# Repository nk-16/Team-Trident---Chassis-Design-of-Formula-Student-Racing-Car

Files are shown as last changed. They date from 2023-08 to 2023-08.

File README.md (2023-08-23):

# Team-Trident---Chassis-Design-of-Formula-Student-Racing-Car

<div style="text-align: justify;">
This project is under  Team Trident, SAE Collegiate Club, IIT(BHU), Varanasi, for the SUPRA SAE competition. This is based on the designing, simulation, and manufacturing of chassis.
</div>

<br>

* **Designing**  <div style="text-align: justify;">I contributed to chassis design in SOLIDWORKS. I learned about new features like planes, weldments, corner treatments, and 3D sketches. Before designing, we went through the rulebook of SUPRA SAE and understood all the constraints so we could design according to them.</div>

<div align="center">
  
</div>

<br>

* **Simulation** <div style="text-align: justify;">I contributed to the chassis simulation in Ansys Mechanical using Finite Element Analysis (FEA) to get stress-strain properties of the chassis. We did front impact testing, side impact testing, and rear impact testing and did hand-in calculations to verify Ansys results.</div>



<br>

* **Manufacturing** <div style="text-align: justify;">  After finalizing the chassis' design and getting suitable results from the simulation, we proceed to its manufacturing. We used AISI 1018 steel pipes and Manual Arc Welding to weld them.</div>



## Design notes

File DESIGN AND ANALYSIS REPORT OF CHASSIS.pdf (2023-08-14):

## DESIGN AND ANALYSIS REPORT OF CHASSIS

Abstract — This Design Report mainly analyzes the Formula Student Racing Car chassis. This chassis is designed by conforming to the rules of SUPRA SAE 2023. The chassis frame is the main structural component to which all the other parts are attached. The chassis frame acts as the skeleton of the automobile, so it should withstand various load conditions. FEA Analysis conforms to the ability to assess the forces and safety of design before manufacturing. The material Preferred for this chassis is AISI 1018, which has good strength and ductility and low weight and is economically viable. The analysis is done on standard Results to get the maximum strength and minimum weight possible. The software tool used for designing is SOLIDWORKS, and for analysis is ANSYS.

INTRODUCTION

The SAE competition comprises static and dynamic events, where the teams are judged based on various parameters, such as conforming to the rules, the vehicle's performance, teamwork, and vehicle compliance. The safety of the driver in the cockpit is of utmost importance. Hence, FEA analysis is carried out by considering various loads, such as bending, torsion, twisting, side impact, and front impact.

The FSAE chassis undergoes various forces during the dynamic event, and FEA analysis helps decide the manufacturing process needed to make the chassis as rigid as possible with minimal cost. Material selection also plays a vital role in strength and torsional rigidity. Therefore, the FEA analysis helps optimize the design and material selection to achieve the desired stiffness and stability while keeping costs low.

The paper focuses on the results of the analysis of the chassis used in the FSAE competition. Here we first explain the methodology of analysis and material property. Then, we will explain analysis calculations and simulation results when the chassis is used with front impact, side impact, rear impact, and torsional stiffness by the rules of the SUPRA SAE competition.

METHODOLOGY

The process typically begins with the team researching and analyzing the regulations set by SUPRA SAE, including weight and size limitations, safety requirements, and performance goals.
We then use this information to create a conceptual chassis design, refined and optimized using CAD software.

Once the design was finalized, we analyzed the chassis using finite element analysis (FEA) through ANSYS to ensure it met strength and stiffness requirements and safety regulations. FINITE ELEMENT ANALYSIS (FEA) [1] (https://www.ansys.com/en-in/blog/fundamentals-of-fea-meshing-for-structural-analysis) is carried out to determine the stiffness of the chassis frame before construction. Conventionally in FEA, the frame is subdivided into mesh elements. These meshes are further divided into nodes. Many elements are possible for a structure, and every choice the analyst makes can affect the results. The number, orientation, and size of elements and loads and boundary conditions are critical to obtaining meaningful and accurate values of chassis stiffness. While doing FEA, we chose tetrahedral elements for meshing and kept the average element size at 10 mm. We did conduct a mesh convergence study by also testing results at an element size of 5 mm. We didn't observe quite a deviation, so we finalized the element size to be kept as 10 mm for simplification in computation.

After finalizing the design, the designing team works with the manufacturing team to ensure that the chassis can be produced within the specified budget and manufactured to the highest quality Standards.

After our research, we optimized the dimensions of the chassis.

### 1. Wheelbase = 1589.14 mm 2. Mass = 32.85 kg 3. Material = AISI 1018

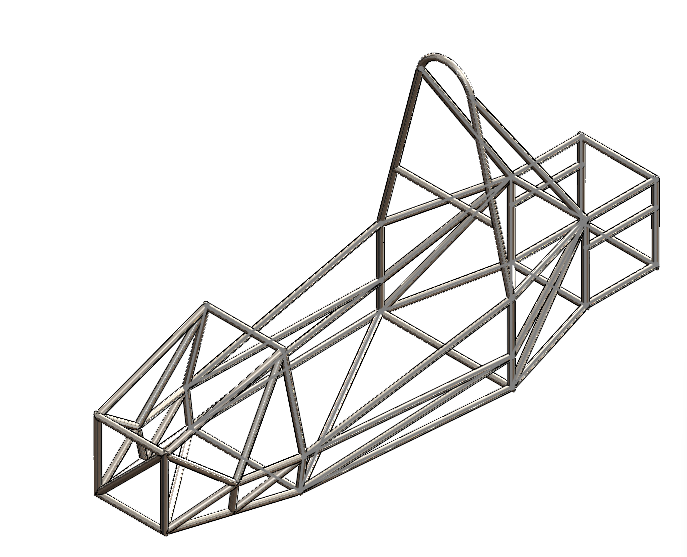
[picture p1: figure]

Fig 1: Isometric view of chassis

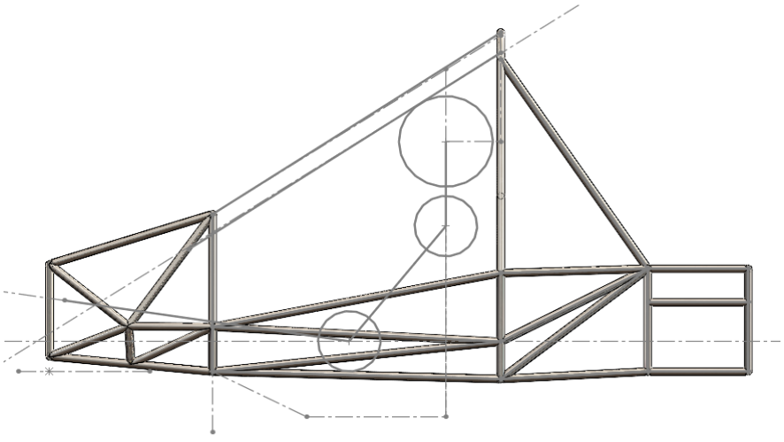
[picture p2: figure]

Fig 2.1: Side view of chassis with a sketch of 95th percentile man

DESIGN PROCESS

We began designing our chassis in September 2023. The Final draft and all analyses were completed by December 2023. The procurement of material and its manufacturing will be completed by February 2023. Hence in this section, the stages of our design have been discussed in detail.

1.) Understanding constraints and subsequent steps

We first go through the rulebook of SUPRA SAE and understand the constraints like:-

- Triangulation of all members in chassis
- Height of main hoop and front hoop
- Minimum wheelbase
- Size of side impact members
- Angles of the main hoop and front hoop
- Distance between firewall and engine
- Specifications of 95th percentile male and 50 mm rule
1.1) We started our sketch-making wheelbase and respective planes for the main hoop, front hoop, rear hoop, front bulkhead, and impact attenuator. Initially, we took a wheelbase of 1800 mm, but later, altering the positions of the hoops and changing the leg angle to 95th percentile male, we finalized at 1589.14 mm. Then we draw all

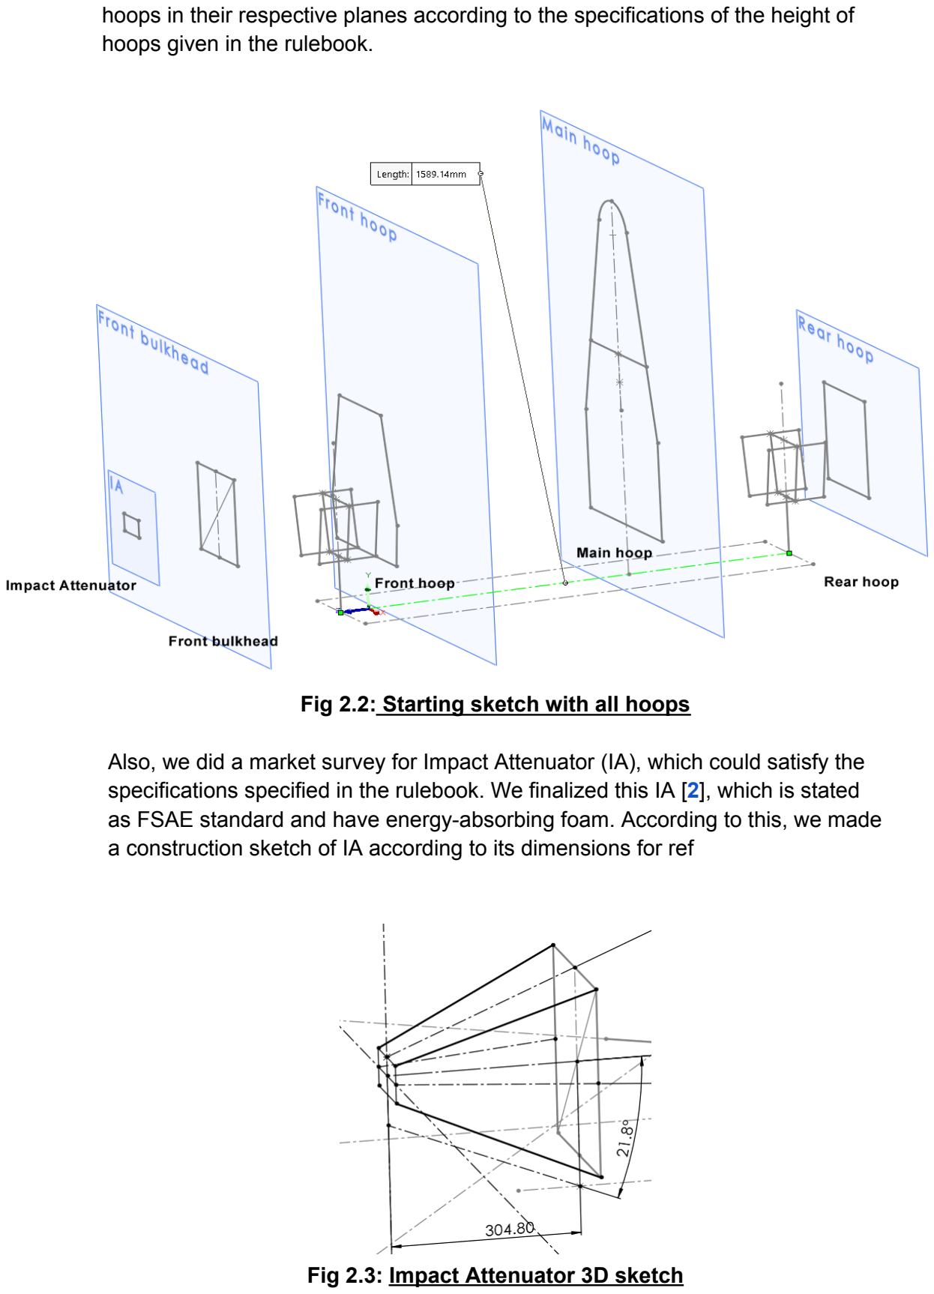
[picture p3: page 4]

hoops in their respective planes according to the specifications of the height of hoops given in the rulebook.

Fig 2.2: Starting sketch with all hoops

Also, we did a market survey for Impact Attenuator (IA), which could satisfy the specifications specified in the rulebook. We finalized this IA [2], (https://pdf.indiamart.com/impdf/16297415162/MY-4624662/fsae-spec-standard-impact-attenuator.pdf) which is stated as FSAE standard and have energy-absorbing foam. According to this, we made a construction sketch of IA according to its dimensions for ref

Fig 2.3: Impact Attenuator 3D sketch

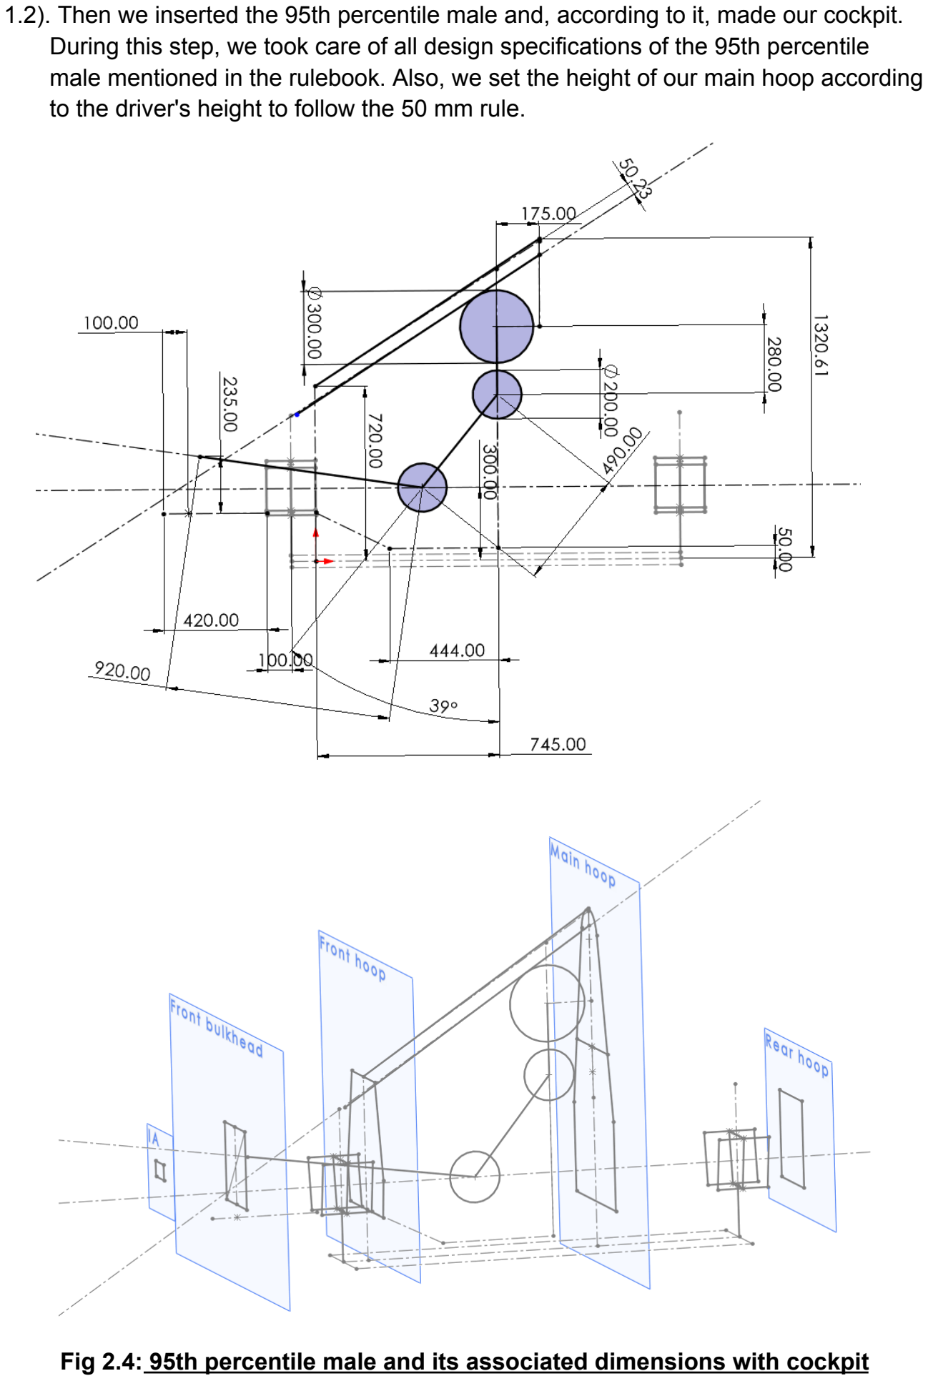
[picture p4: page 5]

1.2). Then we inserted the 95th percentile male and, according to it, made our cockpit. During this step, we took care of all design specifications of the 95th percentile male mentioned in the rulebook. Also, we set the height of our main hoop according to the driver's height to follow the 50 mm rule.

Fig 2.4: 95th percentile male and its associated dimensions with cockpit

1.3) We draw the trusses in between hoops. We first draw the side impact
members between the main and front hoops to complete the cockpit. After this, we complete the trusses between other hoops. The trusses between the front hoop and front bulkhead have been altered after analysis of each cad model in ansys.

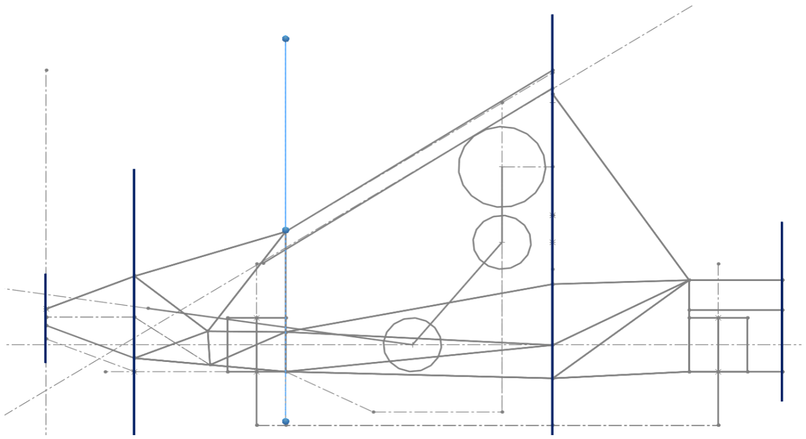
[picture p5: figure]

Fig 2.5: Side view of chassis sketch with a sketch of 95th percentile man

1.4) As per the rulebook, we use custom weldment profiles to have proper AISI 1018 pipes of the correct diameter and thickness. Then we do corner treatment using the trim/extend feature to refine all chassis corners.

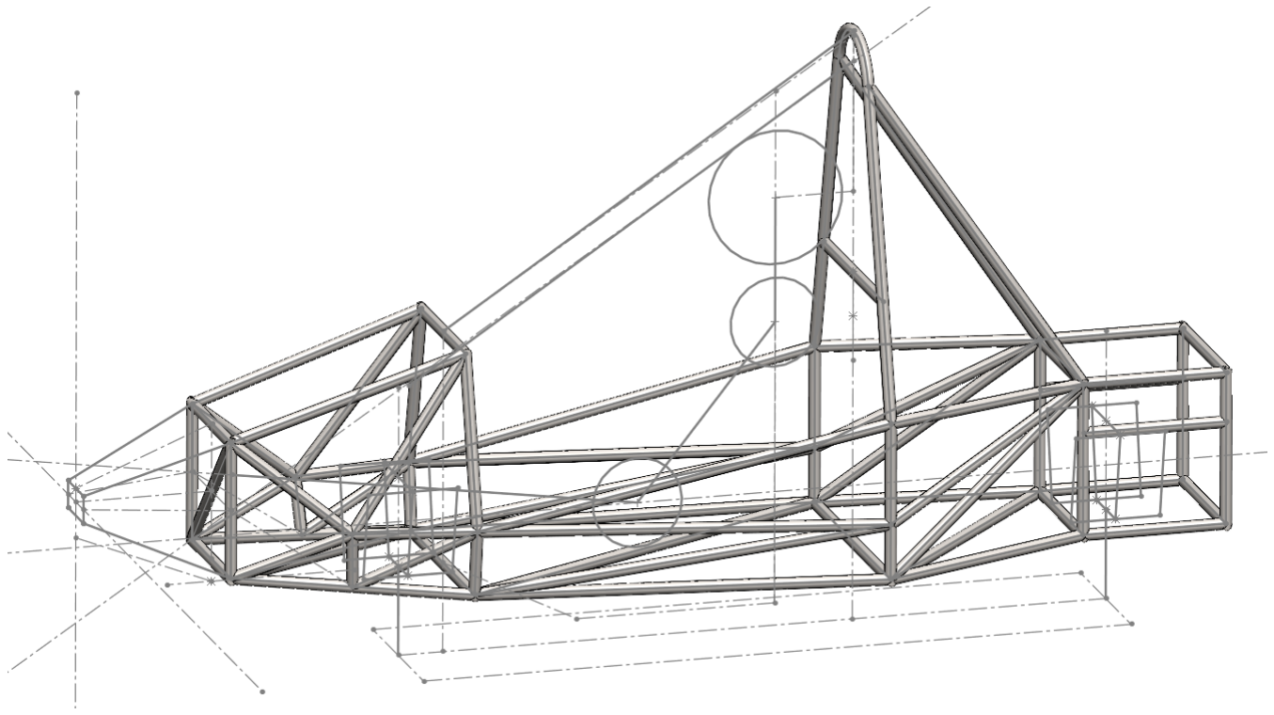
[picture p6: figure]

Fig 2.5: Chassis after insertion of custom weldments and cornertreatments

2.) Optimization of chassis design

We try to optimize the design of the chassis based on the following parameters: -

- Weight of chassis
- Height of the main hoop
- Aerodynamics

As explained in a later section, we test our CAD models in ANSYS to optimize these parameters. According to the results of those analyses, we made changes in our chassis and finalized these parameters.

2.1) Weight of chassis - We optimize the weight of chassis by 15% by reducing additional members of chassis which are not required as stress concentration on them is low.

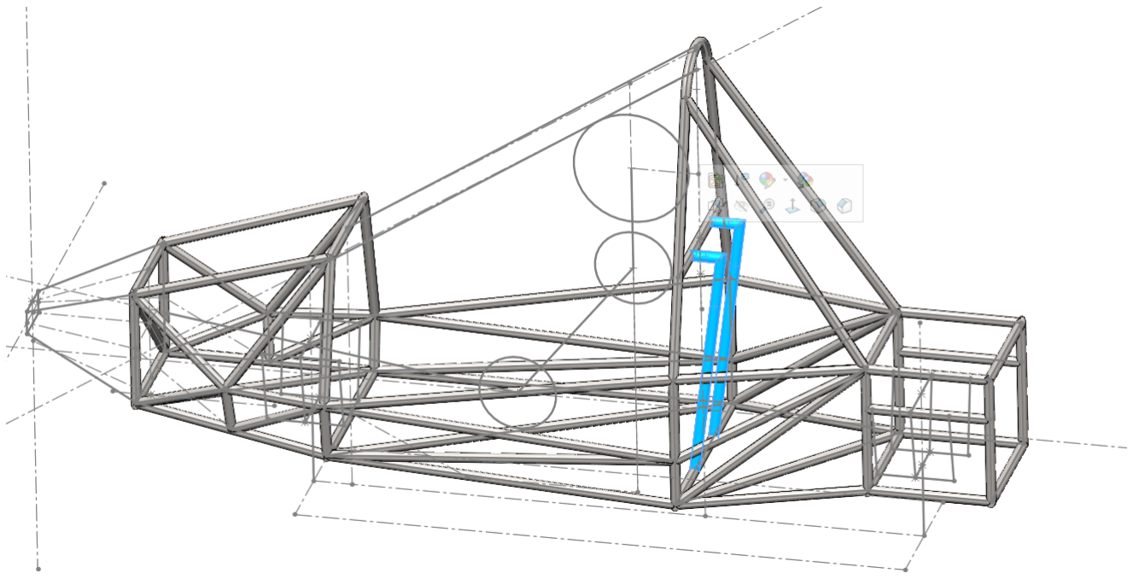
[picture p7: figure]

Fig 2.6: Chassis with extra shoulder harnesses in blue colour

For example, we initially designed these highlighted rods to strengthen the shoulder harness. Still, we did a stress-strain analysis on the chassis without these highlighted members and got good results. Hence we removed it and optimized the weight of our chassis.

2.2) Height of the main hoop - We need to optimize the height of the main hoop because as its height increases, the torsional stress also increases [3]. (https://www.academia.edu/64896073/Modelling_analysis_of_high_effect_of_roll_hoop_main_on_the_strength_of_student_car_formula_chassis) But also, the main hoop height should be enough to accommodate the engine inlet valve. Keeping these two factors in mind, we finalize the height of the main hoop.

MATERIAL SELECTION

The material selected for the Chassis is AISI 1018. AISI 1018 is a low-carbon steel commonly used in manufacturing due to its excellent weldability, machinability, and formability. Here are some properties [4]: (https://www.azom.com/article.aspx?ArticleID=6115)

1. Chemical Composition: AISI 1018 contains 0.18% carbon, 0.6-0.9% manganese, 0.04% phosphorus, and 0.05% sulfur.

### 2. Mechanical Properties: The tensile strength of AISI 1018 ranges from 410-790

MPa, while its yield strength is between 250-550 MPa. It has a hardness of 121-229 Brinell.

### 3. Physical Properties: AISI 1018 has a density of 7.87 g/cm³, a melting point of

1425-1540°C, and a thermal conductivity of 51.9 W/mK.

### 4. Machinability: AISI 1018 has excellent machinability due to its low carbon

content, which makes it easy to cut, drill, and weld.

### 5. Weldability: AISI 1018 can be welded using various welding methods, including

MIG, TIG, and stick welding.

### 6. Formability: AISI 1018 can be easily formed into different shapes using

cold-working processes such as bending, punching, and rolling.

### 7. Corrosion Resistance: AISI 1018 has poor corrosion resistance and is

susceptible to rusting if not adequately protected.

Properties | Metric
Tensile Strength, Ultimate | 440 MPa
Tensile Strength, Yield | 370 MPa
Modulus of Elasticity | 205 GPa
Bulk Modulus | 140 GPa
Shear Modulus | 80 GPa
Poisson’s Ratio | 0.29
Table 1.0 - Properties of AISI 1018 [4] (https://www.azom.com/article.aspx?ArticleID=6115)

ANALYSIS

After selecting the material, the next task is to analyze the design. Two types of analysis are done on a vehicle. They are static and dynamic analyses. Static analysis is done for the car in the stationary position, and dynamic analysis is done for the vehicle in motion. It will be discussed only on static analysis, as formula student race cars won’t be going at such drastic high speeds.

A. Types of analysis
- Front-impact analysis
- Side impact analysis
- Rear impact analysis
B. Steps for performing analysis

Several softwares are available to analyze the object, such as Hyper Mesh, ANSYS, SOLIDWORKS, etc. And here, analysis has been done on the ANSYS. A few basic and simple steps will be followed to perform all the analyses mentioned above on the designed chassis. They are given as follows:

- Import the design in the ANSYS
- Apply the necessary properties of the material
- Mesh the structure completely
- Apply load at the required portion of the chassis of the car and boundary conditions.
- Note the obtained yield strength value and calculate its Factor of safety (FOS) and other necessary results.

Front Impact analysis

Front Impact Analysis determines the stress distribution throughout the body and the deformation generated in the FSAE chassis if the car hits a rigid body from the front. In contrast, it is more likely to happen in any worst case. To Simulate the frontal impact crash, the vehicle was assumed to impact with a momentum transfer as calculated below.

Calculations:

Parameters | Values
Kerb weight of the car + driver | 270 kg

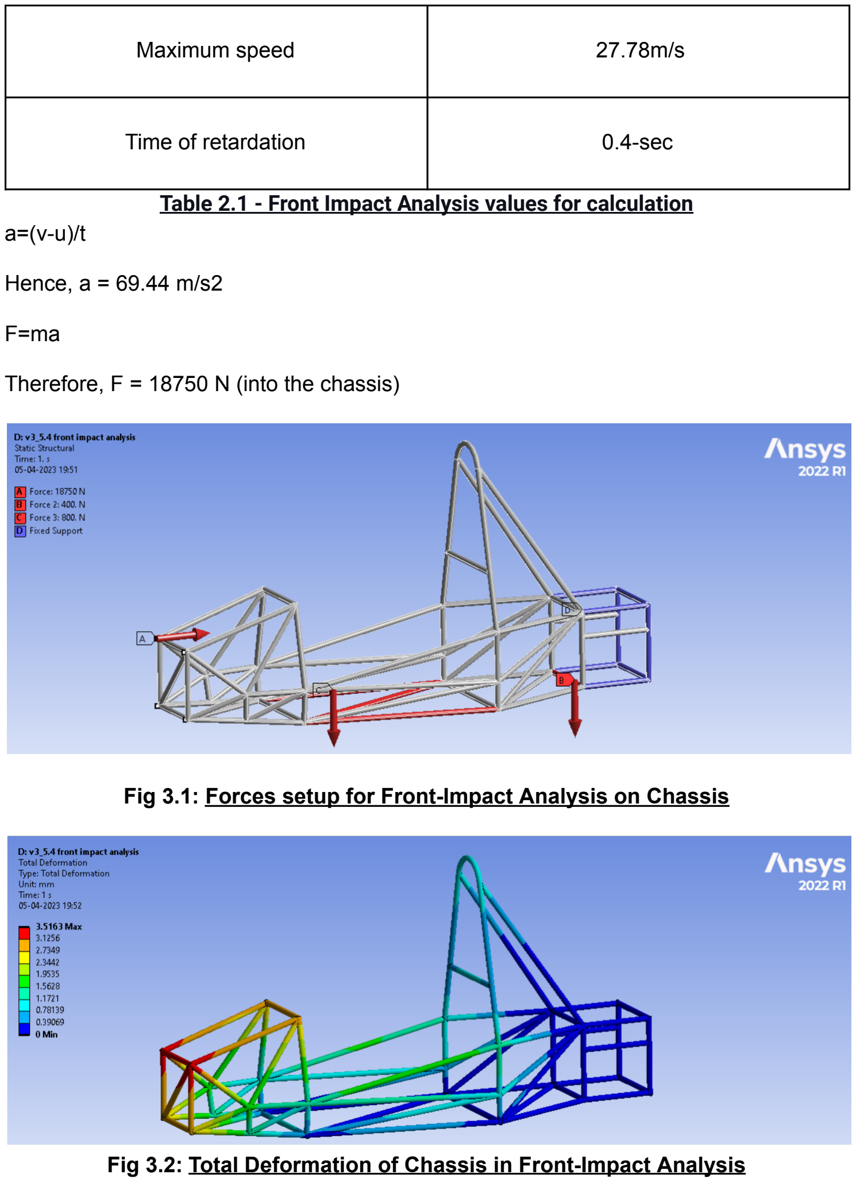
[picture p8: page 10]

Maximum speed | 27.78m/s
Time of retardation | 0.4-sec

Table 2.1 - Front Impact Analysis values for calculation a=(v-u)/t

Hence, a = 69.44 m/s2

F=ma

Therefore, F = 18750 N (into the chassis)

Fig 3.1: Forces setup for Front-Impact Analysis on Chassis

Fig 3.2: Total Deformation of Chassis in Front-Impact Analysis

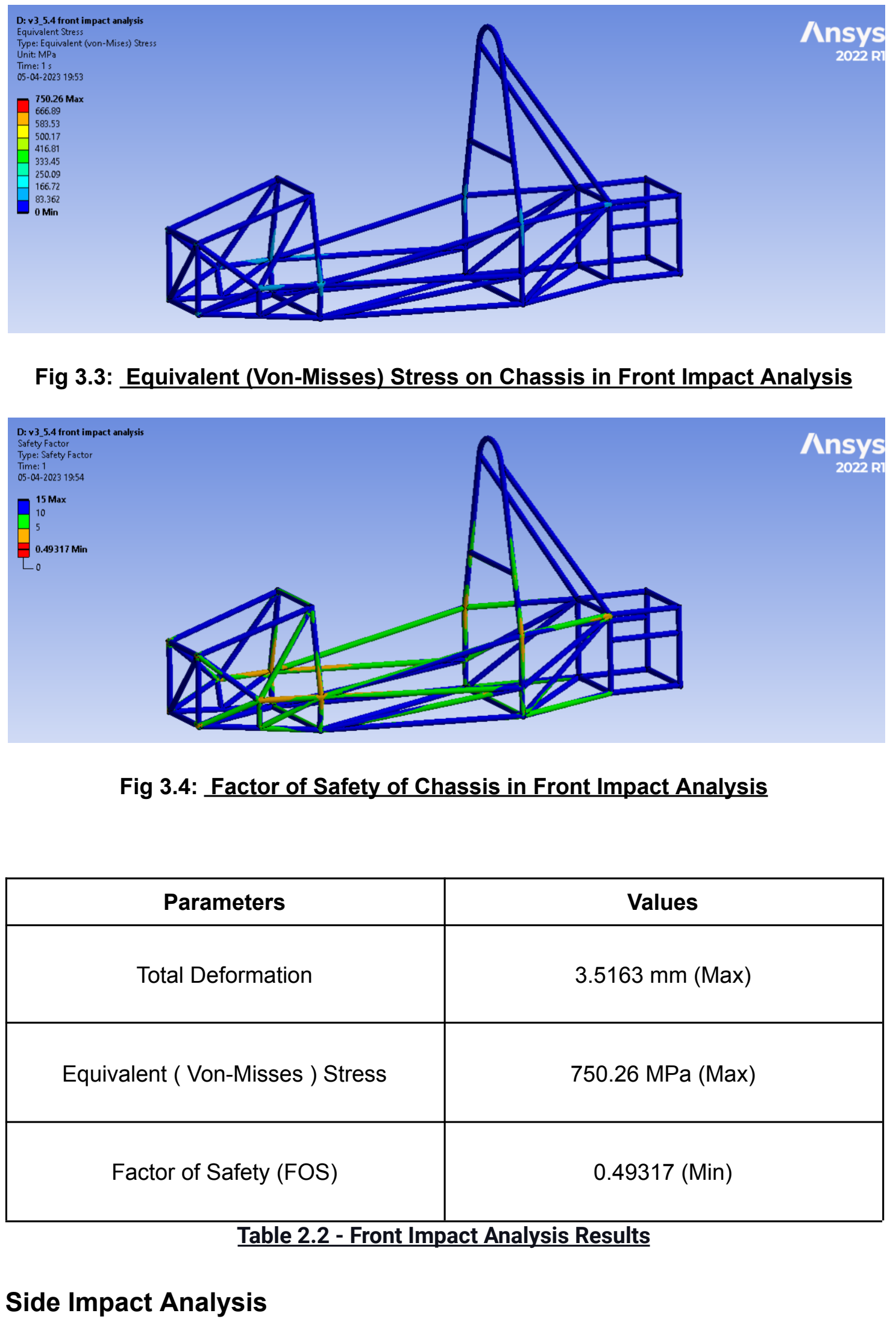
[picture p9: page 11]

Fig 3.3: Equivalent (Von-Misses) Stress on Chassis in Front Impact Analysis

Fig 3.4: Factor of Safety of Chassis in Front Impact Analysis

Parameters | Values
Total Deformation | 3.5163 mm (Max)
Equivalent ( Von-Misses ) Stress | 750.26 MPa (Max)
Factor of Safety (FOS) | 0.49317 (Min)

Table 2.2 - Front Impact Analysis Results

Side Impact Analysis

The side wall of the chassis is resting against the wall, and another vehicle is supposed to collide against it from the opposite side over the same portion. For constraining the chassis, the suspensions are kept fixed.

Calculations:

Parameters | Values
Mass of the car | 270 kg
Maximum speed | 27.78m/s
Time of retardation | 0.4-sec

Table 2.3 - Side Impact Analysis values for calculation

a=(v-u)/t

Hence, a = 39.68 m/s2

F=ma

Therefore, F = 10714.28 N (into the chassis at an angle of 45 degrees)

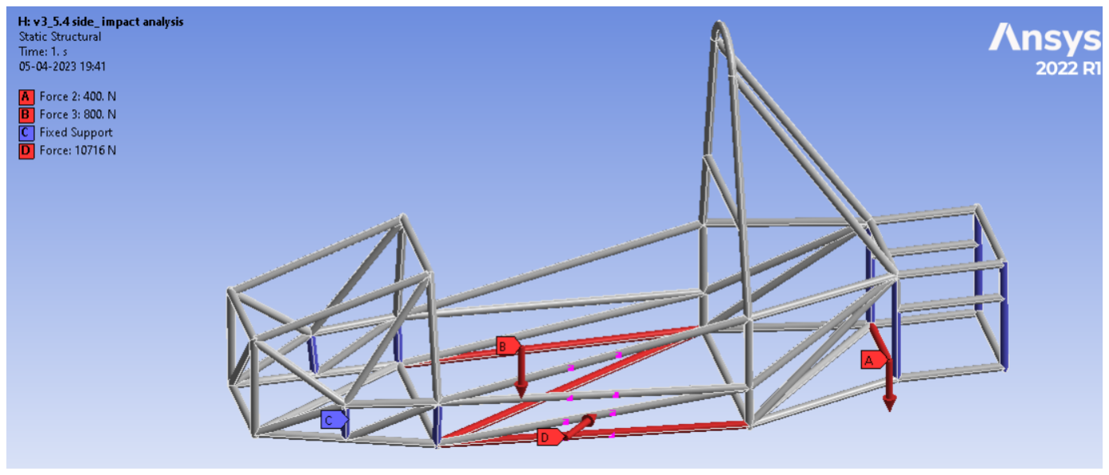
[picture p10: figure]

Fig 4.1: Forces setup for Side-Impact Analysis on Chassis

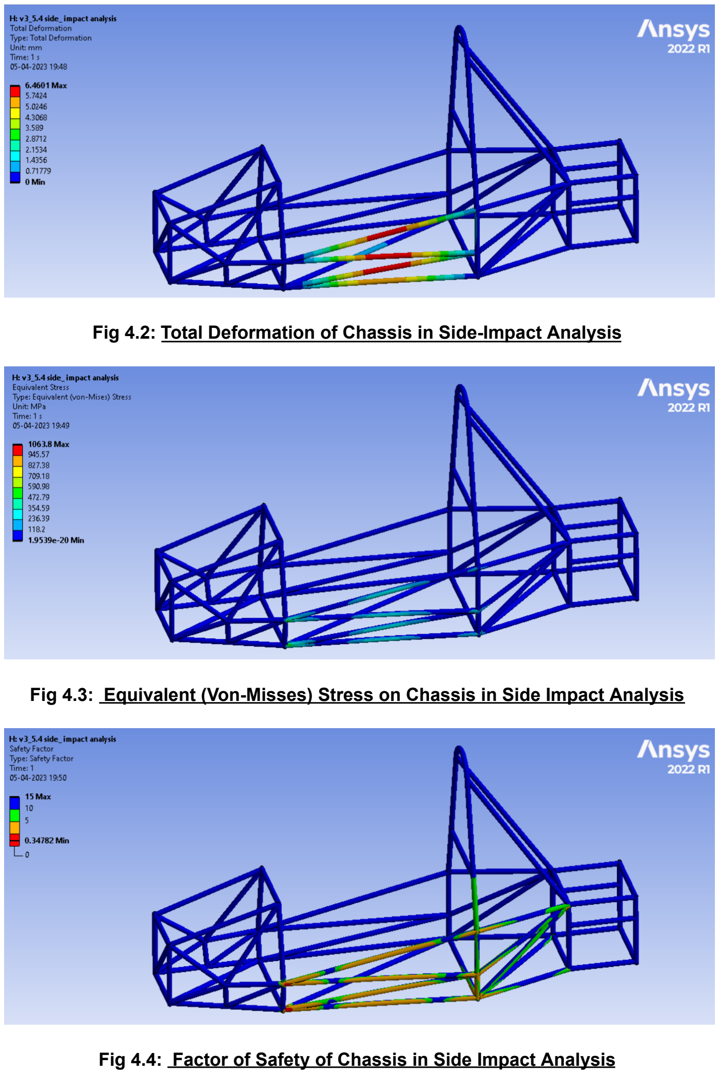
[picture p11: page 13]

Fig 4.2: Total Deformation of Chassis in Side-Impact Analysis

Fig 4.3: Equivalent (Von-Misses) Stress on Chassis in Side Impact Analysis

Fig 4.4: Factor of Safety of Chassis in Side Impact Analysis

Parameters | Values
Total Deformation | 6.46 mm (Max)
Equivalent ( Von-Misses ) Stress | 1063.8 MPa (Max)
Factor of Safety (FOS) | 0.34782 (Min)

Table 2.4 - Side Impact Analysis Results

Rear Impact analysis

The Front Impact Analysis determines the bending stress and deformation generated in the FSAE chassis if the car hits a solid body from the rear end. In contrast, it is more likely to happen in any worst case. To Simulate the rear impact crash, the vehicle was assumed to impact upon a stationary object.

Calculations:

Parameters | Values
Mass of the car | 270 kg
Maximum speed | 27.78m/s
Time of retardation | 0.4-sec

Table 2.5 - Rear Impact Analysis values for calculation

a=(v-u)/t

Hence, a = 69.44 m/s2

F=ma

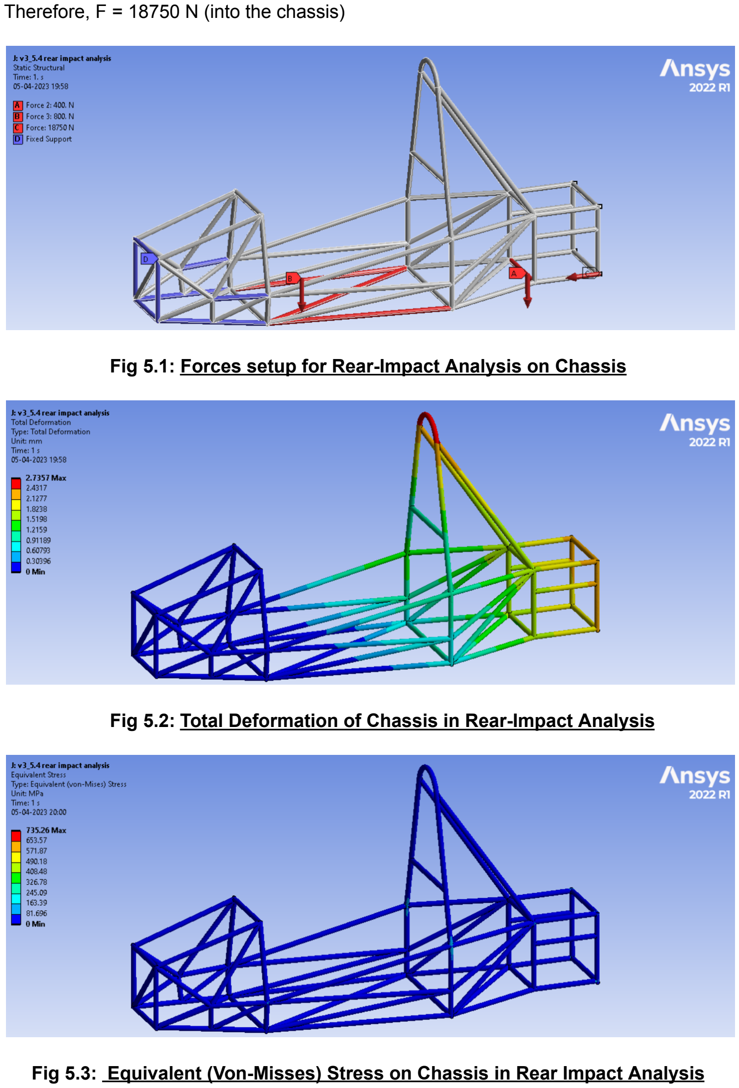
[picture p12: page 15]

Therefore, F = 18750 N (into the chassis)

Fig 5.1: Forces setup for Rear-Impact Analysis on Chassis

Fig 5.2: Total Deformation of Chassis in Rear-Impact Analysis

Fig 5.3: Equivalent (Von-Misses) Stress on Chassis in Rear Impact Analysis

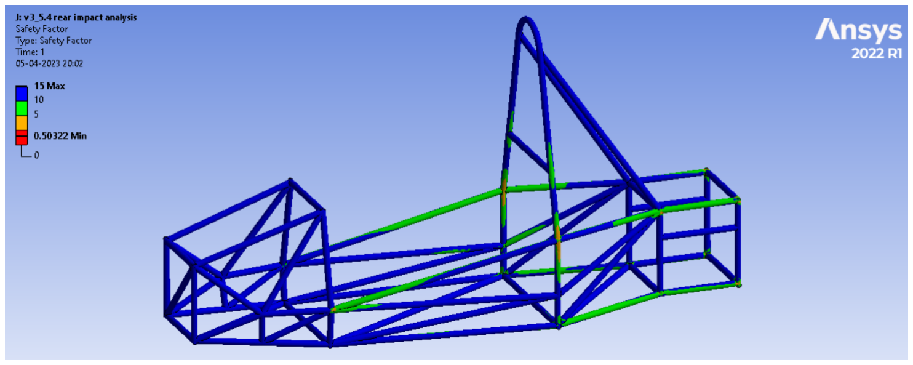
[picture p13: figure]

Fig 5.4: Factor of Safety of Chassis in Rear Impact Analysis

Parameters | Values
Total Deformation | 2.73 mm (Max)
Equivalent ( Von-Mises ) Stress | 735.26 MPa (Max)
Factor of Safety (FOS) | 0.50322 (Min)

Table 2.6 - Rear Impact Analysis Results

REFERENCES

1)https://www.ansys.com/en-in/blog/fundamentals-of-fea-meshing-for-structural-analysis

2)https://pdf.indiamart.com/impdf/16297415162/MY-4624662/fsae-spec-standard-impact -attenuator.pdf (https://pdf.indiamart.com/impdf/16297415162/MY-4624662/fsae-spec-standard-impact-attenuator.pdf)

3)https://www.academia.edu/64896073/Modelling_analysis_of_high_effect_of_roll_hoop_main_on_the_strength_of_student_car_formula_chassis (https://www.academia.edu/64896073/Modelling_analysis_of_high_effect_of_roll_hoop_main_on_the_strength_of_student_car_formula_chassis)

4)https://www.azom.com/article.aspx?ArticleID=6115

5)https://drive.google.com/drive/folders/1oTPhtlNRPRTjwdnBda3W0YMMPyO2GDFK?usp=sharing (https://drive.google.com/drive/folders/1oTPhtlNRPRTjwdnBda3W0YMMPyO2GDFK?usp=sharing) - Chassis files of Team Trident

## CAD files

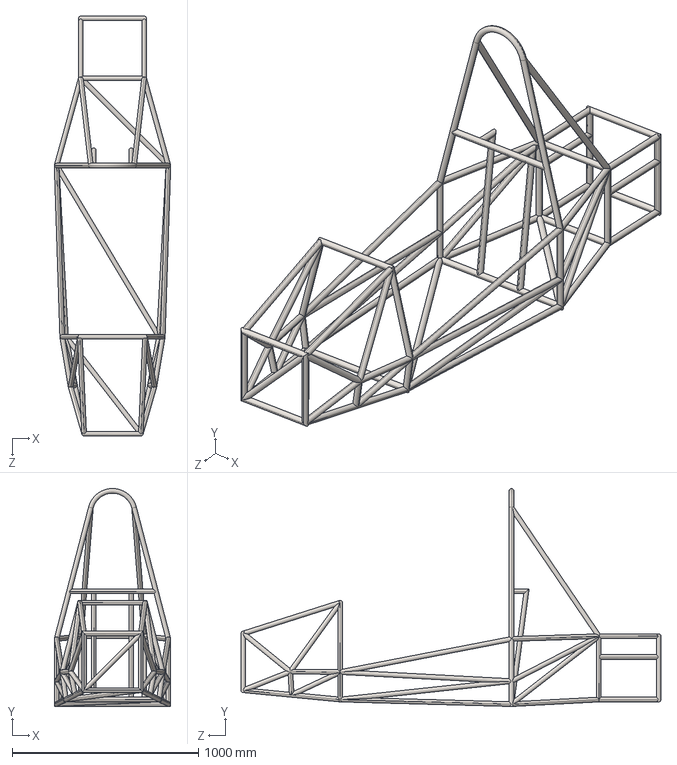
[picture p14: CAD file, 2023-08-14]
chassis_draft_final_corrected_v3_5.3_new.STEP
625.4 x 1170.7 x 2255.4 mm

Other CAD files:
chassis_draft_final_corrected_v3_5.3_new.SLDPRT
